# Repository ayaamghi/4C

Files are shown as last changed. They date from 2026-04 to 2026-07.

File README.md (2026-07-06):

<div align="center">

# 4C

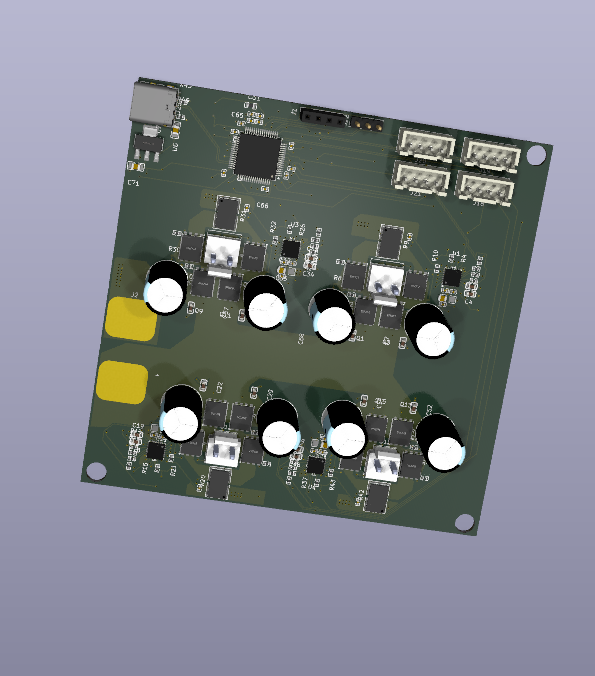
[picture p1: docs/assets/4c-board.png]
4C PCB render





</div>

Four-channel brushed DC motor controller board built around an STM32G4, DRV8701 gate drivers, and discrete MOSFET bridges.

## Layout

- `hardware/kicad/4C.kicad_pro` - open this in KiCad
- `hardware/kicad/libs/` - project-local imported parts and 3D models
- `firmware/cubemx/` - STM32CubeMX config
- `docs/datasheets/` - datasheets and layout notes

Hardware is still in progress; check the schematic, BOM, and fab outputs before ordering.

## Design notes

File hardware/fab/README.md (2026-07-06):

# Fab Outputs

Use this folder for local KiCad/JLCPCB manufacturing exports.

From `hardware/kicad/4C.kicad_pro`, set the plugin/export output path to:

`../fab/jlcpcb`

Generated gerbers, drill files, BOMs, CPLs, reports, and zip files are ignored by git.

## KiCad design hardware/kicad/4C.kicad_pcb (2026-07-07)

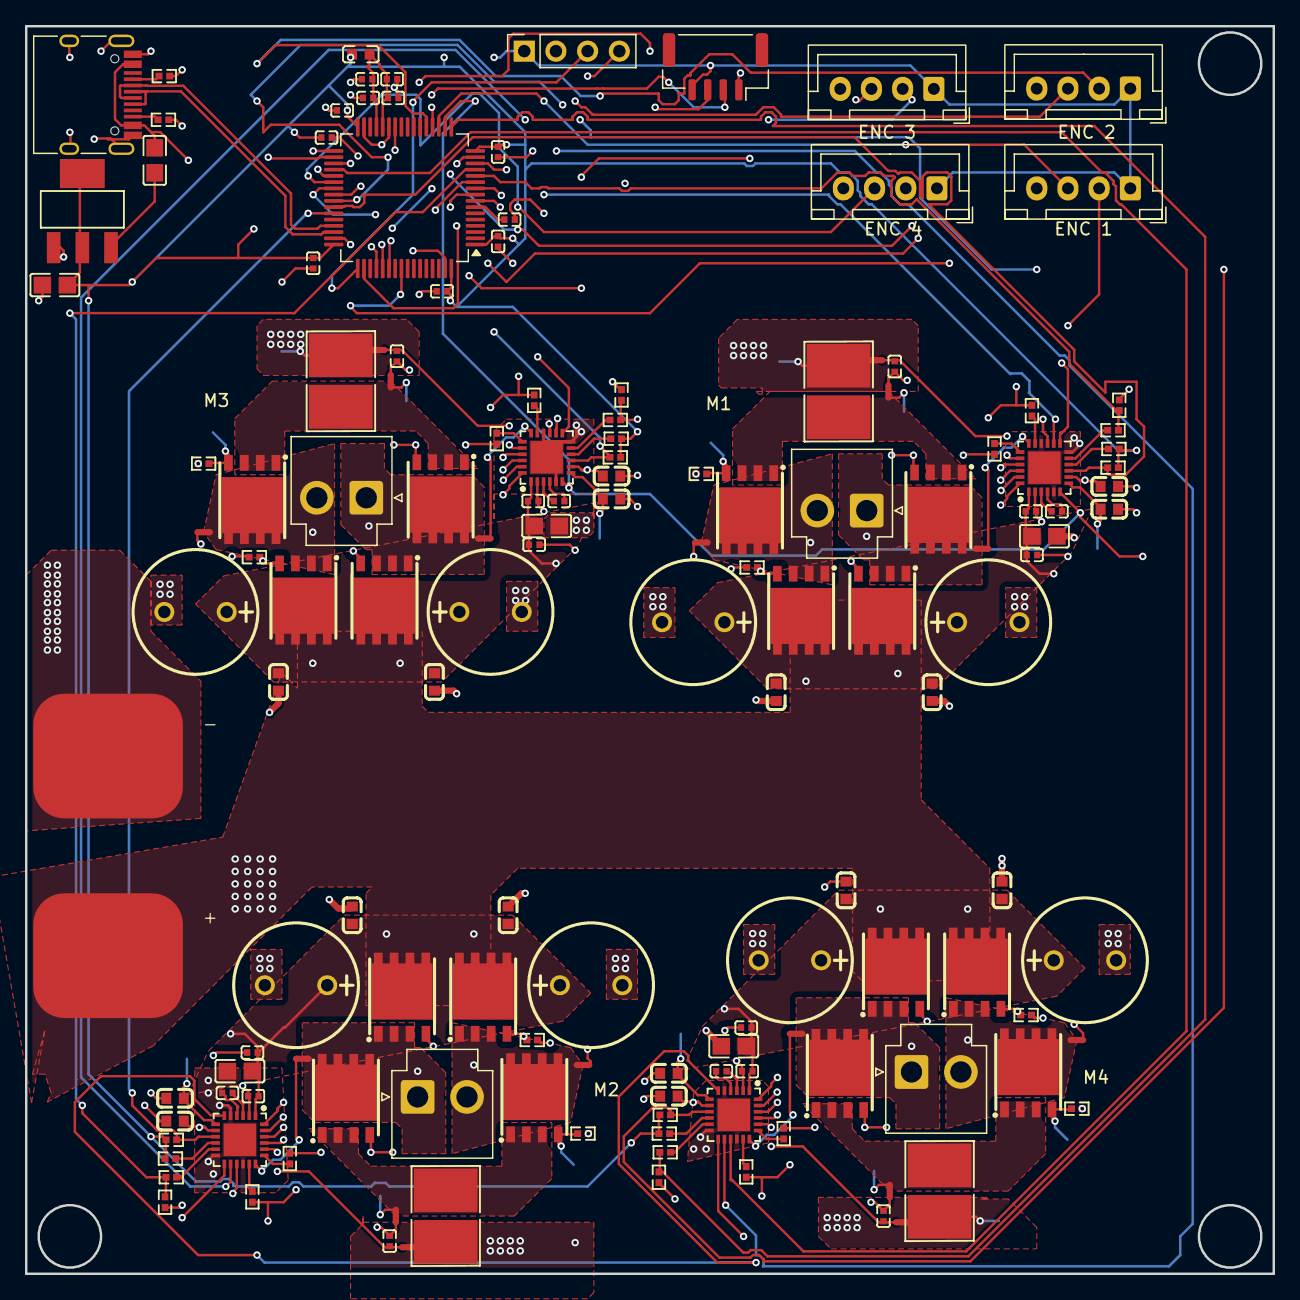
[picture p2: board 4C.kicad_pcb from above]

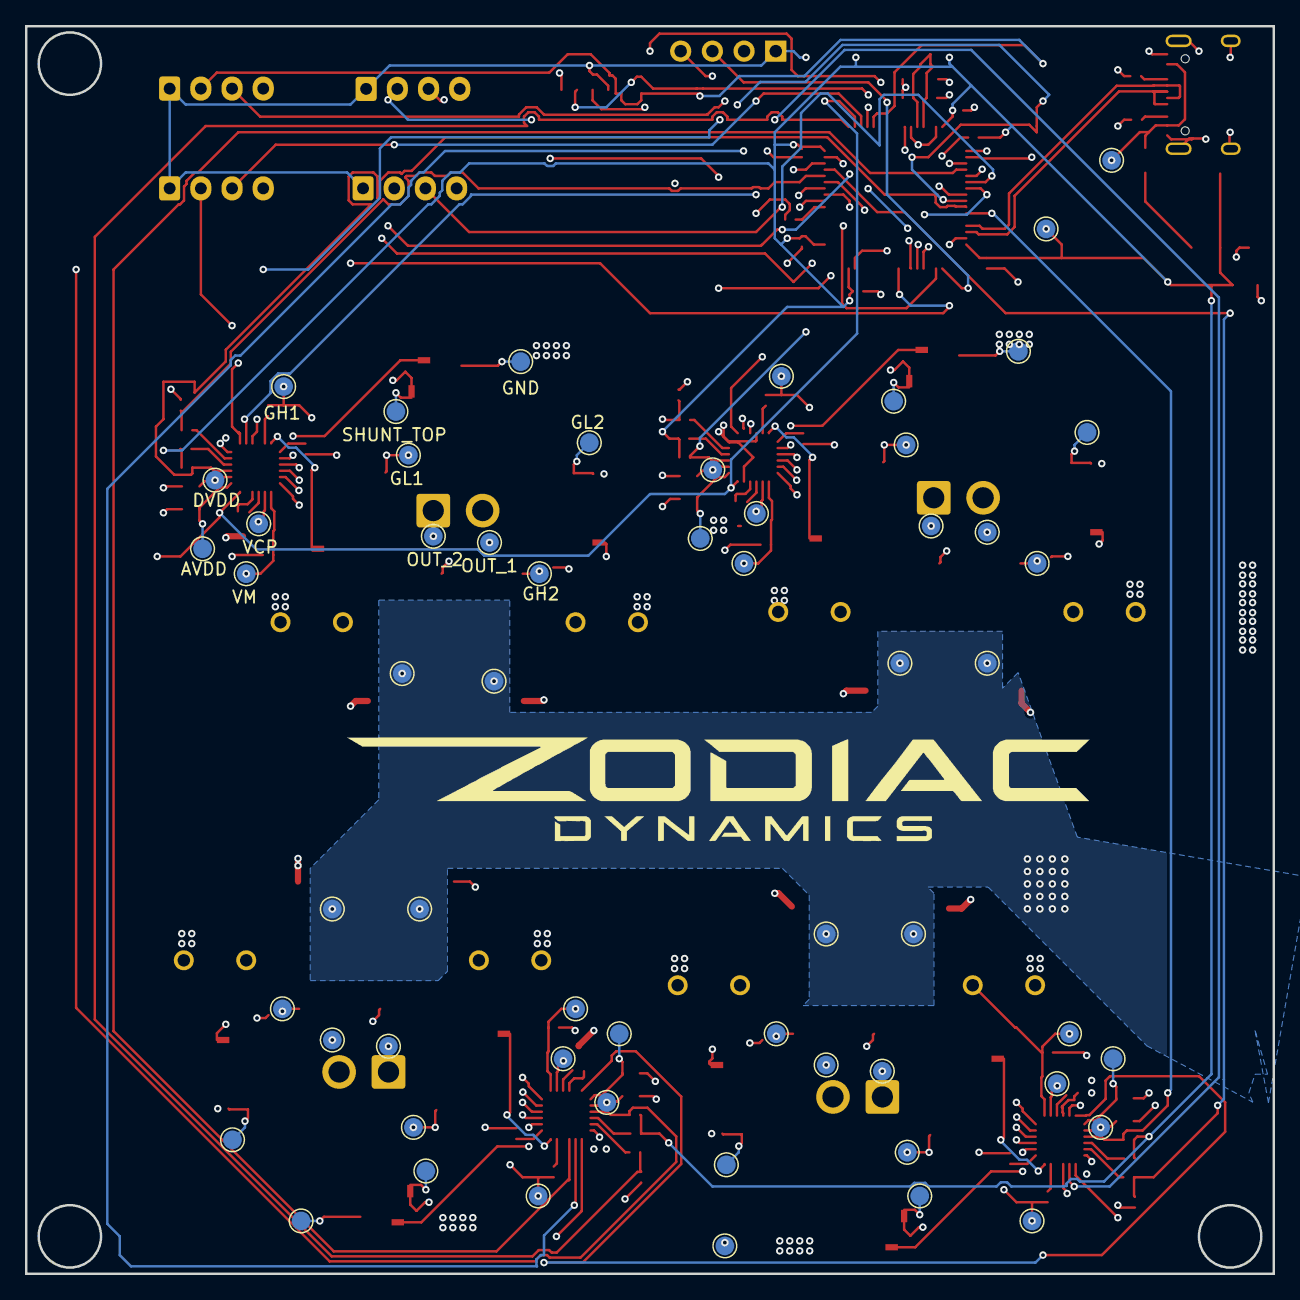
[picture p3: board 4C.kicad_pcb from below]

Board: 4 copper layers, 100.0 x 100.0 mm, 204 parts (58 on the bottom side), 129 nets.

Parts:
C1, C16, C31, C46: GRM32ER71H106KA12L; C0805
C2, C6, C17, C21, C32, C36, C47, C51, C62, C64, C66, C67, C68, C69, C72, C73: C1608X7R1H104K; C0402
C3, C4, C7, C14, C18, C19, C22, C29, C33, C34, C37, C44, C48, C49, C52, C59: GRM188R70J105KA01D; C0603
C5, C20, C35, C50, C61, C63: CL05A105KA5NQNC; C0402
C8, C15, C23, C30, C38, C45, C53, C60: ECA-1HM471; CAP-TH_BD10.0-P5.00-D0.6-FD
C9, C24, C39, C54: GRM155R71C102KA01D; C0402
C65: GRM32ER71H106KA12L; C0402
C70: 10uF; C0805
C71: 22uF; C0805
J1: Conn_01x04; PinSocket_1x04_P2.54mm_Vertical
J2: Conn_01x02; SolderWirePad_2x01_SMD_10x12mm
J10, J11, J12, J13: Conn_01x02; JST_VH_B2P-VH_1x02_P3.96mm_Vertical
J18, J19, J20, J21: Conn_01x04; JST_XH_B4B-XH-A_1x04_P2.50mm_Vertical
J22: Conn_01x04; JST_GH_SM04B-GHS-TB_1x04-1MP_P1.25mm_Horizontal
J25: USB_C_Receptacle_USB2.0_16P; USB_C_Receptacle_HRO_TYPE-C-31-M-12
L1: GZ1608D601TF; L0603
NT1, NT2, NT3, NT4, NT5, NT6, NT7, NT8, NT9, NT10, NT11, NT12, NT13, NT14, NT15, NT16: Net-Tie; NetTie-2_SMD_Pad0.5mm
Q1, Q2, Q3, Q4, Q5, Q6, Q7, Q8, Q9, Q10, Q11, Q12, Q13, Q14, Q15, Q16: CSD18540Q5B; VSON-CLIP-8_L5.0-W6.0-P1.27-BL
R1, R2, R4, R12, R13, R15, R23, R24, R26, R34, R35, R37: CRCW060310K0JNEA; R0402
R3, R14, R25, R36: CRCW06037K50JNEA; R0402
R7, R8, R10, R11, R18, R19, R21, R22, R29, R30, R32, R33, R40, R41, R43, R44, R45, R46: CRCW06030000Z0EA; R0402
R9, R20, R31, R42: CRA2512-FZ-R010ELF; R2818
TP1, TP2, TP15, TP16, TP29, TP30, TP43, TP44: VM; TestPoint_Pad_D1.5mm
TP3, TP4, TP5, TP6, TP7, TP8, TP9, TP10, TP11, TP12, TP13, TP14, TP17, TP18, TP19, TP20, TP21, TP22, TP23, TP24, TP25, TP26, TP27, TP28, TP31, TP32, TP33, TP34, TP35, TP36, TP37, TP38, TP39, TP40, TP41, TP42, TP45, TP46, TP47, TP48, TP49, TP50, TP51, TP52, TP53, TP54, TP55, TP56: AVDD; TestPoint_Pad_D1.5mm
TP57, TP58: TestPoint; TestPoint_Pad_D1.5mm
U1, U2, U3, U4: DRV8701ERGER; VQFN-24_L4.0-W4.0-P0.50-BL-EP2.5
U5: STM32G474RETx; LQFP-64_10x10mm_P0.5mm
U6: AMS1117-3.3; SOT-223-3_L6.5-W3.4-P2.30-LS7.0-BR

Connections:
+3.3V: C65.1, C66.1, C67.1, C68.1, C69.1, C71.1, C73.1, J1.1, J18.1, J19.1, J20.1, J21.1, J22.4, L1.1, R1.1, R2.1, R12.1, R13.1, R23.1, R24.1, R34.1, R35.1, TP58.1, U5.1 (VBAT), U5.16 (VDD), U5.32 (VDD), U5.48 (VDD), U5.64 (VDD), U6.2 (VOUT), U6.4 (VOUT)
+5V: C70.2, J25.A4 (VBUS), J25.A9 (VBUS), J25.B4 (VBUS), J25.B9 (VBUS), TP57.1
/D+: J25.A6 (D+), J25.B6 (D+), U5.46 (PA12)
/D-: J25.A7 (D-), J25.B7 (D-), U5.45 (PA11)
/ENC_1_A: J18.3, U5.19 (PA5)
/ENC_1_B: J18.2, U5.56 (PB3)
/ENC_2_A: J19.3, U5.20 (PA6)
/ENC_2_B: J19.2, U5.21 (PA7)
/ENC_3_A: J20.3, U5.26 (PB2)
/ENC_3_B: J20.2, U5.54 (PC12)
/ENC_4_A: J21.3, U5.38 (PC6)
/ENC_4_B: J21.2, U5.39 (PC7)
/EN_1: U1.14 (EN/IN2), U5.8 (PC0)
/EN_2: U2.14 (EN/IN2), U5.9 (PC1)
/EN_3: U3.14 (EN/IN2), U5.10 (PC2)
/EN_4: U4.14 (EN/IN2), U5.11 (PC3)
/PH_DIR_1: U1.15 (PH/IN1), U5.33 (PB11)
/PH_DIR_2: U2.15 (PH/IN1), U5.34 (PB12)
/PH_DIR_3: U3.15 (PH/IN1), U5.35 (PB13)
/PH_DIR_4: U4.15 (PH/IN1), U5.36 (PB14)
/SO_1: R3.1, R4.1, U5.12 (PA0)
/SO_2: R14.1, R15.1, U5.13 (PA1)
/SO_3: R25.1, R26.1, U5.14 (PA2)
/SO_4: R36.1, R37.1, U5.17 (PA3)
/UART_RX: J22.2, U5.53 (PC11)
/UART_TX: J22.3, U5.52 (PC10)
/VREF: U1.6 (VREF), U2.6 (VREF), U3.6 (VREF), U4.6 (VREF), U5.18 (PA4)
/drh1/AVDD: C3.1, TP3.1, U1.7 (AVDD)
/drh1/DVDD: C4.2, TP4.1, U1.8 (DVDD)
/drh1/GH1: R10.1, U1.17 (GH1)
/drh1/GH2: R7.2, U1.24 (GH2)
/drh1/GL1: R11.1, U1.19 (GL1)
/drh1/GL2: R8.2, U1.22 (GL2)
/drh1/OUT1: J10.2, NT1.2, Q1.1 (S), Q1.2 (S), Q1.3 (S), Q2.5 (D), Q2.6 (D), Q2.7 (D), Q2.8 (D), TP8.1
/drh1/OUT2: J10.1, NT4.2, Q3.1 (S), Q3.2 (S), Q3.3 (S), Q4.5 (D), Q4.6 (D), Q4.7 (D), Q4.8 (D), TP10.1
/drh1/SH1: NT4.1, U1.18 (SH1)
/drh1/SH2: NT1.1, U1.23 (SH2)
/drh1/SHUNT_TOP: NT2.1, Q2.1 (S), Q2.2 (S), Q2.3 (S), Q4.1 (S), Q4.2 (S), Q4.3 (S), R9.2, TP9.1
/drh1/SNSOUT: R1.2, U1.10 (SNSOUT)
/drh1/S_N: C9.2, NT3.2, U1.20 (SN)
/drh1/S_P: C9.1, NT2.2, U1.21 (SP)
/drh1/VCP: C5.1, TP2.1, U1.2 (VCP)
/drh2/AVDD: C18.1, TP17.1, U2.7 (AVDD)
/drh2/DVDD: C19.2, TP18.1, U2.8 (DVDD)
/drh2/GH1: R21.1, U2.17 (GH1)
/drh2/GH2: R18.2, U2.24 (GH2)
/drh2/GL1: R22.1, U2.19 (GL1)
/drh2/GL2: R19.2, U2.22 (GL2)
/drh2/OUT1: J11.2, NT5.2, Q5.1 (S), Q5.2 (S), Q5.3 (S), Q6.5 (D), Q6.6 (D), Q6.7 (D), Q6.8 (D), TP22.1
/drh2/OUT2: J11.1, NT8.2, Q7.1 (S), Q7.2 (S), Q7.3 (S), Q8.5 (D), Q8.6 (D), Q8.7 (D), Q8.8 (D), TP24.1
/drh2/SH1: NT8.1, U2.18 (SH1)
/drh2/SH2: NT5.1, U2.23 (SH2)
/drh2/SHUNT_TOP: NT6.1, Q6.1 (S), Q6.2 (S), Q6.3 (S), Q8.1 (S), Q8.2 (S), Q8.3 (S), R20.2, TP23.1
/drh2/SNSOUT: R12.2, U2.10 (SNSOUT)
/drh2/S_N: C24.2, NT7.2, U2.20 (SN)
/drh2/S_P: C24.1, NT6.2, U2.21 (SP)
/drh2/VCP: C20.1, TP16.1, U2.2 (VCP)
/drh3/AVDD: C33.1, TP31.1, U3.7 (AVDD)
/drh3/DVDD: C34.2, TP32.1, U3.8 (DVDD)
/drh3/GH1: R32.1, U3.17 (GH1)
/drh3/GH2: R29.2, U3.24 (GH2)
/drh3/GL1: R33.1, U3.19 (GL1)
/drh3/GL2: R30.2, U3.22 (GL2)
/drh3/OUT1: J12.2, NT9.2, Q9.1 (S), Q9.2 (S), Q9.3 (S), Q10.5 (D), Q10.6 (D), Q10.7 (D), Q10.8 (D), TP36.1
/drh3/OUT2: J12.1, NT12.2, Q11.1 (S), Q11.2 (S), Q11.3 (S), Q12.5 (D), Q12.6 (D), Q12.7 (D), Q12.8 (D), TP38.1
/drh3/SH1: NT12.1, U3.18 (SH1)
/drh3/SH2: NT9.1, U3.23 (SH2)
/drh3/SHUNT_TOP: NT10.1, Q10.1 (S), Q10.2 (S), Q10.3 (S), Q12.1 (S), Q12.2 (S), Q12.3 (S), R31.2, TP37.1
/drh3/SNSOUT: R23.2, U3.10 (SNSOUT)
/drh3/S_N: C39.2, NT11.2, U3.20 (SN)
/drh3/S_P: C39.1, NT10.2, U3.21 (SP)
/drh3/VCP: C35.1, TP30.1, U3.2 (VCP)
/drh4/AVDD: C48.1, TP45.1, U4.7 (AVDD)
/drh4/DVDD: C49.2, TP46.1, U4.8 (DVDD)
/drh4/GH1: R43.1, U4.17 (GH1)
/drh4/GH2: R40.2, U4.24 (GH2)
/drh4/GL1: R44.1, U4.19 (GL1)
/drh4/GL2: R41.2, U4.22 (GL2)
/drh4/OUT1: J13.2, NT13.2, Q13.1 (S), Q13.2 (S), Q13.3 (S), Q14.5 (D), Q14.6 (D), Q14.7 (D), Q14.8 (D), TP50.1
/drh4/OUT2: J13.1, NT16.2, Q15.1 (S), Q15.2 (S), Q15.3 (S), Q16.5 (D), Q16.6 (D), Q16.7 (D), Q16.8 (D), TP52.1
/drh4/SH1: NT16.1, U4.18 (SH1)
/drh4/SH2: NT13.1, U4.23 (SH2)
/drh4/SHUNT_TOP: NT14.1, Q14.1 (S), Q14.2 (S), Q14.3 (S), Q16.1 (S), Q16.2 (S), Q16.3 (S), R42.2, TP51.1
/drh4/SNSOUT: R34.2, U4.10 (SNSOUT)
/drh4/S_N: C54.2, NT15.2, U4.20 (SN)
/drh4/S_P: C54.1, NT14.2, U4.21 (SP)
/drh4/VCP: C50.1, TP44.1, U4.2 (VCP)
/nFAULT_1: R2.2, U1.9 (FAULT), U5.42 (PA8)
/nFAULT_2: R13.2, U2.9 (FAULT), U5.43 (PA9)
/nFAULT_3: R24.2, U3.9 (FAULT), U5.40 (PC8)
/nFAULT_4: R35.2, U4.9 (FAULT), U5.41 (PC9)
/nSLEEP: U1.13 (SLEEP), U2.13 (SLEEP), U3.13 (SLEEP), U4.13 (SLEEP), U5.37 (PB15)
GND: C1.2, C2.2, C3.2, C4.1, C7.1, C8.2 (-), C14.1, C15.2 (-), C16.2, C17.2, C18.2, C19.1, C22.1, C23.2 (-), C29.1, C30.2 (-), C31.2, C32.2, C33.2, C34.1, C37.1, C38.2 (-), C44.1, C45.2 (-), C46.2, C47.2, C48.2, C49.1, C52.1, C53.2 (-), C59.1, C60.2 (-), C61.1, C62.2, C63.1, C64.2, C65.2, C66.2, C67.2, C68.2, C69.2, C71.2, C72.2, C73.2, J1.2, J2.1, J18.4, J19.4, J20.4, J21.4, J22.1, J25.A1 (GND), J25.A12 (GND), J25.B1 (GND), J25.B12 (GND), J25.S1 (SHIELD), NT3.1, NT7.1, NT11.1, NT15.1, R4.2, R9.1, R15.2, R20.1, R26.2, R31.1, R37.2, R42.1, R45.2, R46.2, TP11.1, TP25.1, TP39.1, TP53.1, U1.5 (GND), U1.12 (IDRIVE), U1.16 (GND), U1.25 (PAD), U2.5 (GND), U2.12 (IDRIVE), U2.16 (GND), U2.25 (PAD), U3.5 (GND), U3.12 (IDRIVE), U3.16 (GND), U3.25 (PAD), U4.5 (GND), U4.12 (IDRIVE), U4.16 (GND), U4.25 (PAD), U5.15 (VSS), U5.27 (VSSA), U5.31 (VSS), U5.47 (VSS), U5.63 (VSS), U6.1 (GND)
unnamed: J1.3, U5.49 (PA13)
unnamed: J1.4, U5.50 (PA14)
unnamed: J25.A5 (CC1), R45.1
unnamed: J25.B5 (CC2), R46.1
unnamed: Q1.4 (G), R7.1, TP5.1
unnamed: Q2.4 (G), R8.1, TP6.1
unnamed: Q3.4 (G), R10.2, TP13.1
unnamed: Q4.4 (G), R11.2, TP14.1
unnamed: Q5.4 (G), R18.1, TP19.1
unnamed: Q6.4 (G), R19.1, TP20.1
unnamed: Q7.4 (G), R21.2, TP27.1
unnamed: Q8.4 (G), R22.2, TP28.1
unnamed: Q9.4 (G), R29.1, TP33.1
unnamed: Q10.4 (G), R30.1, TP34.1
unnamed: Q11.4 (G), R32.2, TP41.1
unnamed: Q12.4 (G), R33.2, TP42.1
unnamed: Q13.4 (G), R40.1, TP47.1
unnamed: Q14.4 (G), R41.1, TP48.1
unnamed: Q15.4 (G), R43.2, TP55.1
unnamed: Q16.4 (G), R44.2, TP56.1
unnamed: C6.1, U1.3 (CPH)
unnamed: C6.2, U1.4 (CPL)
unnamed: R3.2, U1.11 (SO)
unnamed: C21.1, U2.3 (CPH)
unnamed: C21.2, U2.4 (CPL)
unnamed: R14.2, U2.11 (SO)
unnamed: C36.1, U3.3 (CPH)
unnamed: C36.2, U3.4 (CPL)
unnamed: R25.2, U3.11 (SO)
unnamed: C51.1, U4.3 (CPH)
unnamed: C51.2, U4.4 (CPL)
unnamed: R36.2, U4.11 (SO)
unnamed: C72.1, U5.7 (PG10)
unnamed: C70.1, U6.3 (VIN)
VDDA: C61.2, C62.1, C63.2, C64.1, L1.2, U5.28 (VREF+), U5.29 (VDDA)
VM: C1.1, C2.1, C5.2, C7.2, C8.1 (+), C14.2, C15.1 (+), C16.1, C17.1, C20.2, C22.2, C23.1 (+), C29.2, C30.1 (+), C31.1, C32.1, C35.2, C37.2, C38.1 (+), C44.2, C45.1 (+), C46.1, C47.1, C50.2, C52.2, C53.1 (+), C59.2, C60.1 (+), J2.2, Q1.5 (D), Q1.6 (D), Q1.7 (D), Q1.8 (D), Q3.5 (D), Q3.6 (D), Q3.7 (D), Q3.8 (D), Q5.5 (D), Q5.6 (D), Q5.7 (D), Q5.8 (D), Q7.5 (D), Q7.6 (D), Q7.7 (D), Q7.8 (D), Q9.5 (D), Q9.6 (D), Q9.7 (D), Q9.8 (D), Q11.5 (D), Q11.6 (D), Q11.7 (D), Q11.8 (D), Q13.5 (D), Q13.6 (D), Q13.7 (D), Q13.8 (D), Q15.5 (D), Q15.6 (D), Q15.7 (D), Q15.8 (D), TP1.1, TP7.1, TP12.1, TP15.1, TP21.1, TP26.1, TP29.1, TP35.1, TP40.1, TP43.1, TP49.1, TP54.1, U1.1 (VM), U2.1 (VM), U3.1 (VM), U4.1 (VM)

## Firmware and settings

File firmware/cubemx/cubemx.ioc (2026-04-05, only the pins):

Mcu.UserName=STM32G474RETx
PA0.GPIO_Label=SO_1
PA0.Signal=ADC1_IN1
PA1.GPIO_Label=SO_2
PA1.Signal=ADC1_IN2
PA10.GPIO_Label=PWM_1
PA10.Signal=S_TIM2_CH4
PA11.Signal=USB_DM
PA12.Signal=USB_DP
PA13.Signal=SYS_JTMS-SWDIO
PA14.Signal=SYS_JTCK-SWCLK
PA15.Signal=I2C1_SCL
PA2.GPIO_Label=SO_3
PA2.Signal=ADC1_IN3
PA3.GPIO_Label=SO_4
PA3.Signal=ADC1_IN4
PA4.Signal=COMP_DAC11_group
PA5.GPIO_Label=ENC_1_A
PA5.Signal=S_TIM2_CH1
PA6.GPIO_Label=ENC_2_A
PA6.Signal=S_TIM3_CH1
PA7.GPIO_Label=ENC_2_B
PA7.Signal=S_TIM3_CH2
PA8.GPIO_Label=nFAULT_1
PA8.Signal=GPIO_Input
PA9.GPIO_Label=nFAULT_2
PA9.Signal=GPIO_Input
PB0.GPIO_Label=PWM_3
PB0.Signal=S_TIM3_CH3
PB1.GPIO_Label=PWM_4
PB1.Signal=S_TIM3_CH4
PB10.GPIO_Label=PWM_2
PB10.Signal=S_TIM2_CH3
PB11.GPIO_Label=PH_DIR_1
PB11.Signal=GPIO_Output
PB12.GPIO_Label=PH_DIR_2
PB12.Signal=GPIO_Output
PB13.GPIO_Label=PH_DIR_3
PB13.Signal=GPIO_Output
PB14.GPIO_Label=PH_DIR_4
PB14.Signal=GPIO_Output
PB15.GPIO_Label=nSLEEP
PB15.Signal=GPIO_Output
PB2.GPIO_Label=ENC_3_A
PB2.Signal=S_TIM5_CH1
PB3.GPIO_Label=ENC_1_B
PB3.Signal=S_TIM2_CH2
PB6.GPIO_Label=PWM_5
PB6.Signal=S_TIM4_CH1
PB7.Signal=I2C1_SDA
PB8-BOOT0.Signal=FDCAN1_RX
PB9.Signal=FDCAN1_TX
PC0.GPIO_Label=EN_1
PC0.Signal=S_TIM1_CH1
PC1.GPIO_Label=EN_2
PC1.Signal=S_TIM1_CH2
PC10.Signal=UART4_TX
PC11.Signal=UART4_RX
PC12.GPIO_Label=ENC_3_B
PC12.Signal=S_TIM5_CH2
PC2.GPIO_Label=EN_3
PC2.Signal=S_TIM1_CH3
PC3.GPIO_Label=EN_4
PC3.Signal=S_TIM1_CH4
PC6.GPIO_Label=ENC_4_A
PC6.Signal=S_TIM8_CH1
PC7.GPIO_Label=ENC_4_B
PC7.Signal=S_TIM8_CH2
PC8.GPIO_Label=nFAULT_3
PC8.Signal=GPIO_Input
PC9.GPIO_Label=nFAULT_4
PC9.Signal=GPIO_Input

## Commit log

2026-04-04 completed copying TI ref diagram
    [4CPCB.kicad_sch, drh.kicad_sch]
2026-04-05 pre-STM32 signal routing
    [4CPCB.kicad_sch, drh.kicad_sch, pcb.kicad_pcb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]
